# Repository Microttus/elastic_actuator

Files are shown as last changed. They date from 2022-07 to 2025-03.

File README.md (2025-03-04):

# Elastic Arm

This device was developed and tested during the Haptic Summer School
at UiA for the EMERALD project Autum 2022.

*If you are to publish work base don this project please cite:*

```text
@article{sanfilippo2024open,
  title={Open-source design of low-cost sensorised elastic actuators for collaborative prosthetics and orthotics},
  author={Sanfilippo, Filippo and {\O}kter, Martin and Dale, J{\o}rgen and Tuan, Hua Minh and Zafar, Muhammad Hamza and Ottestad, Morten},
  journal={HardwareX},
  volume={19},
  pages={e00564},
  year={2024},
  publisher={Elsevier}
}
```

## Table of Content

1. [Motivation](#motivation)
1. [Demonstration](#Video)
2. [Intro](#the-haptic-arm-lab)
3. [Code](#code)
4. [CAD](#cad)
5. [How To Use Seeeduino](#implementation-of-seeeduino-in-arduino-ide)
6. [How To Use](#how-to-use)
   - [Instalation](#installation)
   - [Test Code Explanation](#test-code-explanation)

## Motivation

The main goal of this project is to create an easy to build and 
assemble haptic installation which can be controlled as a haptic devise. 
This is made possible by the use of a joint with integrated springs. 
A greater displacement of the motor for a smaller amount of force 
compared to a rigid robotic arm is therefore possible. 

For how to use see: [How To Use](#how-to-use)

## Video
This YouTube video shows an example of both Impedance control and Admittance control was tested:
https://youtu.be/x0tvgowaUfE?si=nHkEfITcb-D-KBVI

## The Haptic Arm Lab

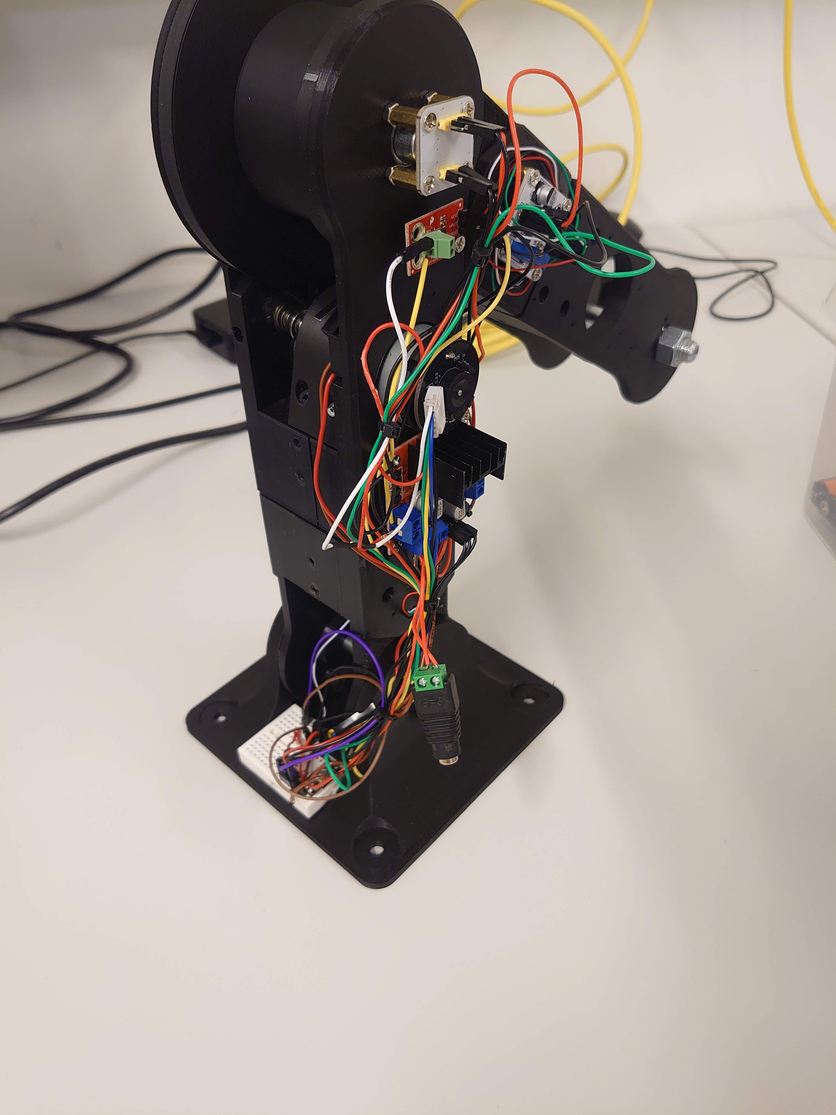
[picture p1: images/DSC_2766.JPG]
Haptic Arm Lab


In Haptic devices, there are two main ways for control. 
Impedance control aim to steer the position by reading the motor force. 
Admittance control aim to control the force of the device by adjusting the position. 
This two are integrated as methods and can be used directly, 
by the use of the low-level libraries this control codes may also be created by the user. 
A descriptive block diagram of the two control loops. 

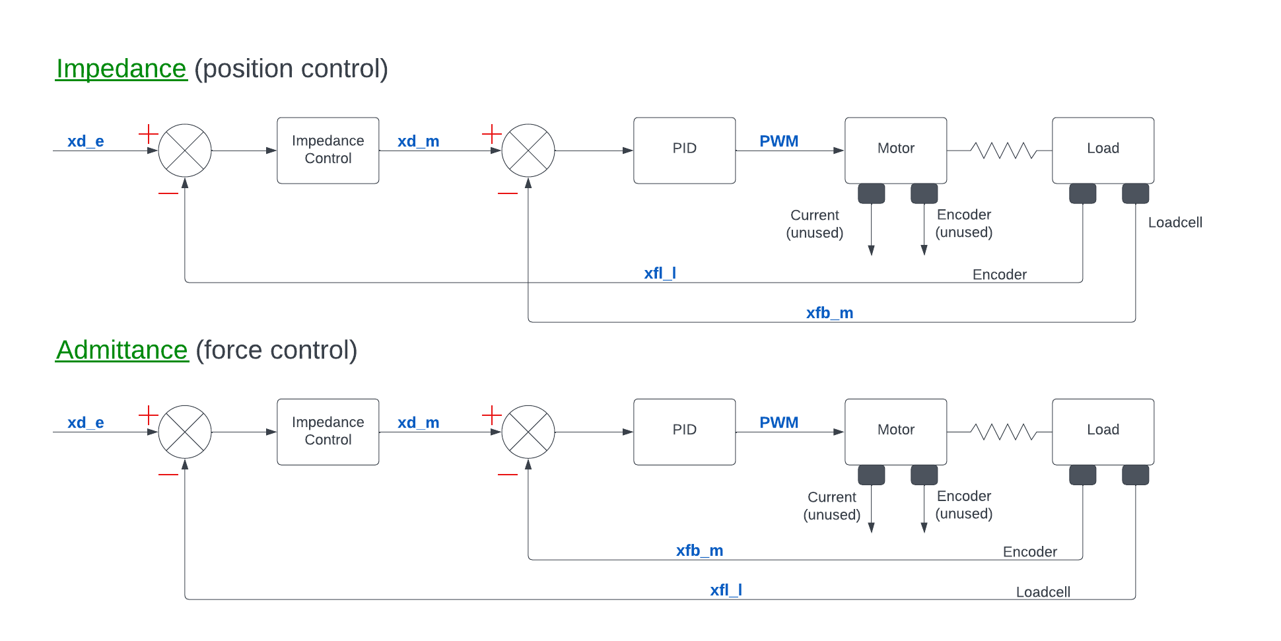
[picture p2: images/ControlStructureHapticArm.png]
Block Diagram


## Code
The code which is to be used can be found in Code.

The main control .ino file can be altered to control the arm in different available modes. The libaries can also be used seperately for control of other mechanical instalation. 

For the Haptic Sommer School course use the studentProgram() implimented into the HapticArm libary for creating own self-produced controlling programs.

For more documentation of the system more detiled information can be found in the documentation folder. (LINK) The documentation is sectioned into mechanical buildt instruction, electrical components and softwear. In addition a more detaiueld explanation of the control theory is available.

The equations used for the control modes are shown beneath.

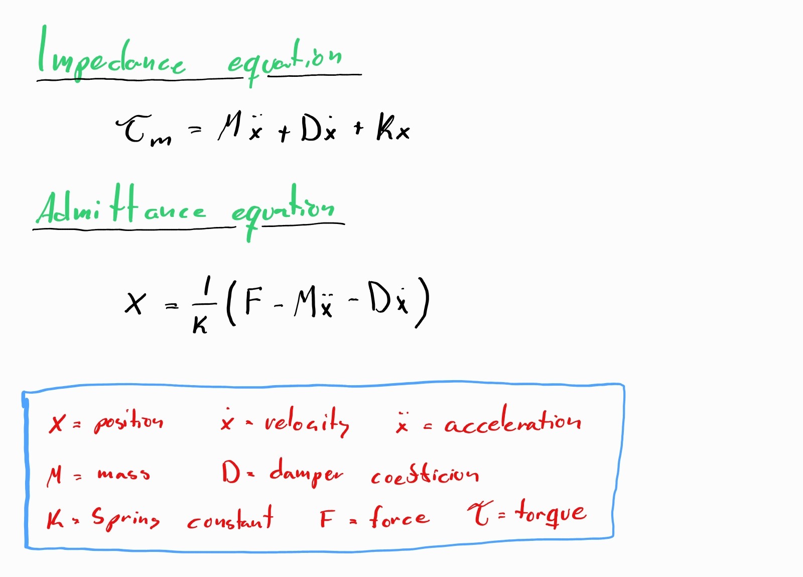
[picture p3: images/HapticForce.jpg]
Force Equations


## CAD
A version off the design can be found in CAD as .stl files ready for printing. In the detailed parts folder the smallest parts and the belt-gear 
which should be printed in higher detail for optimal use, can be found.

## Implementation of Seeeduino in Arduino IDE
To be able to access Seeduino XIAO in the Arduino IDe Board Manager, an "Additional Board Manager URLs:" have to be added in FIle > Preferences:
```
http://files.seeedstudio.com/arduino/package_seeeduino_boards_index.json
```

## How To Use

### Installation

After the complete mechanical assembly is finished and the electronics
mounted as described [here](https://instructions.online/?id=3988-mechanical%20assembly),
the microcontroller of your choice can be plugged into your computer. An IDE for
programming microcontrollers are necessary, the Arduino IDE works perfectly fine and
can be downloaded [here](https://www.arduino.cc/en/software). 

After installing your IDE the seeeduino board programing package have to be added
as described in [Implementation of Seeeduino in Arduino IDE](#implementation-of-seeeduino-in-arduino-ide)
section. 

```text
http://files.seeedstudio.com/arduino/package_seeeduino_boards_index.json
```

Go to Preferences and paste the Url given above into the "Additional board manager URLs:"
box. The seeeduino package should now be available to install from the board manager.

### Test Code

Start by cloning this repository on to your computer. Go to Code->testCode 
folder and open the testCode.ino file in the Arduino IDE. If the microcontroller
is connected, the port should be available in the drop-down menu at the top 
of the window. 

Choose which control method you want to applies by uncommenting the line providing
the selected method. For both ```goImpedance``` and ```goAdmittance``` functions
the three first arguments are respective mass, spring and damper coefficients
for your system. The last argument for impedance is optional and sets the initial
position. If no input are given, 125 degrees, which is the middle, is used. 
The last two arguments for Admittance is optional. The Initial position is 
default middle (125 degrees), and the initial force is 0 that represents the 
force sensitivity of the system. If the initial position is set to -1, the 
arm will hold the current position. This simulates a typical "tech the robot"
mode. 

The ```goPos``` function can be use for basic position control. This function
is used internally in the ```goAdmittance``` and should therefor be carefully 
tuned before moving on to the more advanced control methods. 

### Test Code Explanation

This code provides a basic setup for testing the pre-set control functions.
First, some basic parameters are set up and the hapticArm class used to 
crate an arm object. If any ports on the electronic setup are changed or the 
PID controller needs adjusting, these values can be altered to your preference.

```c++
#include "hapticarm.h"

#include "hapticsensor.h"

// Initiate ports numbers
int motorSetting[5] = {7, 8, 9, 2, 3};    // Pins for motor {forward, backward, PWM, hall_1, hall_2}
int sensorSetting[4] = {1, 0, 6, 10};      // Pins for sensor  {force, current, switch one, switch two}

// PID settings(Kp, Ki, Kd) {position, force, motor} 
float PIDset[3][3] = {{3,3,30},{3,1,0},{0,0,0}};

HapticArm HapArm_(motorSetting, sensorSetting, PIDset);

// Sinus wave
float A = -30;
float B = 0.1;
float dt = 0.0;
```

Every Arduino code contains two functions, the void setup and void loop. 
The setup function is used to setup parameters and input output settings. 
In the test code first a serial port is set up, enabling the serial communication
for feedback to the computer. Additionally, I2C communication is started with 
the ```Wire.begin()``` command. 

The calibration sequence is available in the HaticArm class. 
This actuates the arm to set the correct end switches and
set the encoder values for the end point. This is important since these values
are mapped to the corresponding arm angle which is used for position. 
The encoder limit values are printed in the serial monitor. If the values
are wraped around 0 the encoder chip should be rotated 90 degrees, as wrapping
of the encoder values has not yet been implemented. 

A loop is taken advantage of to set the Arm straight up which provides a 
smoother start for any actuation. This loop is stoped after approximately
10 seconds. Finally a Header to serial monitor with output explanation for the Admittance or
Impedance control function is available. This can be uncommented as needed. 

```c++
void setup() {
  // Initislize importent comunication
  Serial.begin(9600);
  Wire.begin();
  delay(2000);
  HapArm_.calibrateArm(); // If calibration is needed, else should be let out 
  delay(500);

  float curPos = 0;
  float startPos = 125;
  
  // Set arm to middle position
  while (curPos != startPos && dt < 10){
    HapArm_.goToPos(startPos);
    dt = dt + 0.001;
  }
  dt = 0.0;
  
  //Admittance header
  //Serial.println("AcutalPos;SetPos;SpringAngle;Force;RequestedPos;");

  //Impedace header
  Serial.println("AcutalPos;SetPos;MotorReqSpeed;TorqueMes;TorqueCalc;");
  
}
```

The void loop function will constantly run while the microcontroller is powered
on. Here the desired control function is implemented for the Arm object. 
The First line set a sine wave reference which could be used as a set point, for 
instance, seen in the [video](#video). 

The ```goPosition``` uses a basic PID 
control to set the desired position. The ```goImpedance``` function takes 
three required arguments mass, spring and damper coefficient of the system.
Additionally one optional argument can be given, namely the initial position. 
Default is 125 degrees (the middle), but any number between 0–250 can be used. 
The ```goAddmittance``` function takes three required arguments, mass, 
spring and damper coefficient of the system. In addition, two optional 
arguments can be set, initial position and initial force. The Initial position is
default in the middle but can be set to between 0–250. Initial force represents
the force sensitivity and is default 0.

```c++
void loop() {
  // sinewave for setopint reference
  float pos = A*sin(B*dt) + 125;

  // For control with Impedance uncomment this line
  //HapArm_.goImpedance(0, 0, 1);

  // For control with Admittance uncomment this line
  //HapArm_.goAdmittance(0.1,2,0.02,pos);

  // For basic position control uncomment this line
  HapArm_.goToPos(125);
}
```

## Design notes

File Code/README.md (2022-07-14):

# Haptic Arm Code

- The AD5600 libary are used for reading the Rotary Absolutt Encoder via I2C and are created by:
- The PID libary delivers different methods for PID calcuation and are created as objects
- The PWM motor libary are a compleate libary created for controlling a PWM motor in both directions (CW, CCW) and reading a attached incremental encoder
- The HaapticSensor libary are a range of methods for reading the spesific sensores attached to the Haptic Arm
- The HapticArm libary contains a range of methods for compleate control of the Haptic Arm using all the libaries metioned above

## HapticArm Libary

- The goToPos method makes use of a PID controller and the encoders for maintaing the position of the Arm at a sertain deegree from 0
- The goToImpedance method enable for impecace (position - position) control of the Haptic arm, maintaning a requested angle
- The goToAdmittance method enable for admittance (force - position) control of the Haptic arm, maintaning a requested force

- The resistForce makes the arm maintain the given position with the goToPos method until the force barrier given are breached, then the arm gived in and change position
- The goSpring method makes the Arm change its position form the given staring position acting like a spring with the given mass, dmaper and spring constant given
- The calicaration method makes use of the two presure switches for calibration of max and min calibration of the encoder

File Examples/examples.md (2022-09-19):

# Examples

In this folder multiple folders of exaple program testing the reach of the Haptic Arm can be found

In each program the nessesary libaries to add for full operation are lised

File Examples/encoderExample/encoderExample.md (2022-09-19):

# Encoder Example

For reading and adjusting the output of a encoder sensor readings

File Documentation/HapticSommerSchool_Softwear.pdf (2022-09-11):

# 1 Softwear

The software are build as modular as possible, for easy operation of the arm for a user with any programming background. The course are meant to be applied for students with some to none experience in programming and control theory, and at the same time give experienced personnel the possibility to conduct testing of advanced control theory applied. For a less experienced user, the steering library can be used where only the control factor numbers are to be adjusted. A more experienced user may build the control part itself for the implementation of other steering methods. The basic libraries for data collection can be adjusted and modified by an experienced user for optimal control, higher precision and further development of the system.
The software consist of five classes. The AS5600 library is provided by Seed-Studio for easy reading of data from the absolute magnetic encoder. There are three low level classes, the PID, pwmMotor and HapticSensor classes, which are made for data retrieving and control of the haptic arm on a hard code level. The final library, the HapticArm, contains a range of control methods based on control theory using the mentioned classes above for control of the arm.

## 1.1 AS5600

The AS5600 library is created and distributed by Seed-Studio, which is the producer of the encoder used in this project. The data are retrieved using I2C and memory access and the code are therefore manageable but too complicated to learn if you are not interested in the code side. The library gives the user an easy-to-use interface, retrieving the magnets position. This library needs to be put inside the programming folder or the main Arduino library folder for the program to work.

### 1.1.1 getRawAngle()

The getRawAngle is the only method used of this library. The command return the position of the magnet as a 12 bit signal (0-4095).

## 1.2 PID

The PID class are made for easy implementation of PID loops. It takes advantage of the object properties of classes for the user to easily be able to create multiple loops with different PID values based on the same class. The PID class have three public method in addition to the constructor. One which gives the possibility of a standard PID loop using Kp, Ki and Kd and one which provide the possibility of a PID controller with back calculation integration as an anti wind-up method. The last one is a complimentary filter which are used as a low pass filter on the sensor data. The PID method uses the same values and can be switch during operation if needed.

### 1.2.1 PID(float Kp_in, float Ki_in, float Kd_in)

The PID constructor is used to initialize the PID object. The constructor take Kp, Ki and Kd as input and a single PID object are intended to be used for a single PID loop. The values of the PID block cannot be changed during operation.

### 1.2.2 caluclate(float value, float target)

The calculate method is used if a standard PID loop are intended to be used. This method do not have an anti wind-up integrated. The PID equation used are the standard European method, see equation 1.1. The method have the current value intended to be used and the target as input. The aim target may be changed during operation, which is a key feature for the use of control systems.

The loop time is calculated for every loopback by the object for precision loop calculation. This make the object independent of the clock frequency or the loop time. And the code may stagger without the PID failing, taking advantage of the variable loop time calculation.

ud(k) = Kpe(k) + Ki(ui−1 + e(k) · dt) + Kd

e(k) − ud−1
dt | (1.1)

ud is calculated value, e(k) is the error of the system, ui is calculated integral constant and dt the time step.

### 1.2.3 backcalc(float value, float target, float backVal, float satutaionMin, float

saturationMax)

The backcalc method use the same equation as the calculation method, as well as iterate over the same loop time and uses the same Kp, Ki and Kd. These properties make it possible for the user to switch between these two methods. The value are the current value input for the calculation and the target value are the target for the calculation. In addition to these two, the backVal input is used for tuning the anti wind-up section. The saturtionMin and saturationMax inputs are used for the upper and lower limit for the anti wind-up.
The anti wind-up constant could be set to 1 which would work great. This method should be used as the final loop before sending the value to the motor. If this is the case, an upper limit of 255 and lower -255 is advised, corresponding to the upper and lower limit for PWM.
In the backcaluc method, the integral part of the PID calculation are switched with this equation 1.2.

ud(k) = Kpe(k) + Ki(ui−1 + (e(k) + ep(k) − ud−1 T

) · dt) + Kd

e(k) − ud−1
dt | (1.2)

ep is the saturated ud and T is the back calculation value

### 1.2.4 compfilter(float in_val, float alpha)

The compfilter method is integrated as a way to use the equation for complimentary for values. The complimentary filter may be used as a low-pass filter or high-pass filter, depending on the inn-values. A low-pass filter can be essential for readable sensor-data. The in_val are the new data from the sensor used for calculation. A separate PID object should be initialized for every sensor in the system needing a filter. The earlier results are remembered by the object, and the same object cannot be used for different sensor-data. The alpha constant is the tuning value for the filter. This decides how much the new values are to be weighted. This value is set to 0.01 as standard and do not need to be given for this value, unless a different number is to be used.
The method return the final calculated value. The equation used is 1.3.
ud = (1 − α) · ud−1 + α · e(k) | (1.3)

## 1.3 pwmMotor

The pwmMotor class are a collection of different method used for control of a PWM motor using a H-brigde style motor controller and collect data from a hall encoder. The class consist of five public methods in addition to two private ones and the constructor. The two private methods are used for the collection of data as interrupt from the hall encoder and are set to ”static void” as all methods interacting with interrupt variables do need to be of this data type. This is also the reason for the “static void” data type of the reset_hall_val method.

1.3.1 pwmMotor(int forwardPin_in, int backwardPin_in, int pwm_in,
int hallPinOne_in, int hallPinTwo_in)

The constructor of the pwmMotor class have five inputs for correct setup of the connection between the microchip and the motor controller. The first two inputs are the microchip pins, which are to be connected to the directional control of the motor. These pins are used for digital signals. The third is the pin which the PWM signal are sent to. The last two are the pins which the hall sensor pins are connected. Mark: On Arduino Due the only two pins supporting interrupt are 0 and 1.

### 1.3.2 goToSpeed(int motorSpeed)

This method is the main method used for control of the motor. The method receives the motor speed as an integer. Inside the method, the number will be limited to -255 to 255 to ensure the value do not exceed the capabilities of the microchip. The Arduino Due have an 8 bit DAC and these values are preset for this intent, but may be adjusted if a different chip set is to be used.
If motorSpeed is negative the method will spin the motor backward and on the contrary if the value is positive the motor is spun forward. The method also check if the value is equal to the last value asked. The operation of changing direction may be more time conceiving than just adjust the PWM sequence. Checking if the value have changed and immediately break if the value are the same, saves computational time. A value of -1 for backward and one for forward, are additionally commutated and saved for the intent of being able to check the motor direction elsewhere in the code. This is used for the emergency brake.

### 1.3.3 stop()

The stop method immediately set both directional control pin to zero, and then adjust the PWM signal to zero as well. In this configuration, the motor will run free, which is the optimal configuration if the arm have hit something and need to be stopped immediately. This method is used by the emergency break due to endstops, but may also be implemented if the arm is used for obstacle avoidance or as a cobot.

### 1.3.4 check_rotation()

The check_rotation method return the angle of the arms based on the number of trigger events from the hall sensor interrupt routines. While reading the count, the interrupt routine have to be temporarily paused. This means that for every iteration of the method, steps may be missed.

### 1.3.5 reset_hall_val()

This method is used by the calibration method of the arm. At the end of the calibration sequence, the arm is situated at angle 0. Since the motor encoder is incremental, a fixed start position is necessary. The interrupt will start counting as soon as the motor object is initialized, and the count have to be zeroed at a known location. The calibration routine calls this method in the known zero position, which set both trigger event counts to zero.

### 1.3.6 return_motor_dir()

The value saved by the goToSpeed method is internal, and the return_motor_dir method can be called to read the current value. This is used by the end stop emergency stop. The motor direction value is used for the trigger event detection as well.

## 1.4 HapticSensor

The Haptic Arm have five types of sensors which are integrated into the platform. The motor encoder is implemented in the pwmMotor library. The remaining four are the data collected through this library. The AS5600 library is used for the reading of the absolute position encoder. The library consist of five methods in addition to the constructor. Four are the methods for returning sensor data, and the last one is for configuration of the end positions of the arm for the position sensor.

### 1.4.1 HapticSesor(int forcePin, int currentPin, int switchPinOne, int switch-

PinTwo)

The HapticSensor constructor takes four inputs, which are the pins which the sensors are connected to. ForcePin is the pin for the load cell, which has to be connected through an instrument amplifier and are read as an analogue signal. The currentPin is the pin connected to the current sensor, which is read as an analogue signal as well. switchPinOne and switchPinTwo are the pin which the signal side of the endstops. In the constructor, all the input pins are set as inputs, and the analogue read resolution set to 10 bit.

### 1.4.2 readForce()

The readForce method return the force exposed to the end of the arm. The signal read from the load cell is adjusted due to a graph found through testing with known weights at the connection point on the arm. The force is calculated from the weigh and adjusted for the current angle of the arm for neglecting the weight of the swing arm. The value is adjusted with a low pass filter via the PID library before returned as a float.

### 1.4.3 readPos()

The readPos method use the AS5600 library to retrieve the absolute position of the arm from the magnetic encoder. The belonging angle is calculated and returned as a float. The calculation use the values found by the calibration sequence for the value of the magnetic encoder at the endstops.

### 1.4.4 readCurrent()

This method read the value provided by the current sensor, which is situated between the motor and the motor controller. The signal is converted from a bit value into volt and adjusted for the signal at zero current, roughly in the middle. The volt signal is then multiplied with the amp per volt value given for the sensor. A low-pass filter using a PID block are used to smooth out the signal. The current is returned as a float.

### 1.4.5 readSwitch()

The readSwitch method update both values in the list containing the state of the two endstop switches connected. And finally returning these as a pointer to the list. Therefore, the data type int* is used. The list need to be initiated as a class object and not initialized in the object, as the list in that case would be saved in the stack (which is temporary) and removed when the method returns.

### 1.4.6 calibrateEncoder(int newMinVal, int newMaxVal)

The values for the magnetic absolute encoder are saved as object parameters, such that the calibration sequence is not absolutely necessary if the values for a specific configuration are well known. These values are set in the constructor. After the calibration sequence, the found values are used to change these private values by the use of the calibrateEncoder method. The method return the current raw bit value of the magnetic encoder for the intent of using it during calibration. The argument are optional, but the values will be set to 0 if no value is provided.

## 1.5 HapticArm

The HapticArm library is a class combining the lower lever control classes of the Haptic Arm with the intent of controlling the arm using control theory. The library consist of four public and four private methods in addition to the constructor. The of the private method two are calculating the moved length, speed, and acceleration based on the current and part position using numerical mathematics and the same as angles. The mathematics used for the calculation are shown in equation ??. The last two are the emergency protocols witch read data to ensure the arm have a reasonable behaviour and engage the stop routines if not.

### 1.5.1 HapticArm(int motorSettings[ ], int sensorSettings[ ], int PIDset[ ][3])

The HapticArm constructor takes two list and one multidimensional list as input. The first list are the values used to set up the motor object, in total four values. The object for using the other classes are set up inside this class, which means that all necessary values have to be delivered by this object as a middle man. As a way to avoid having 15-20 input for the object, it is initialized with lists. The second list are the values for the sensor class, and need five objects. The constructor do not need to know the size of the list, but enough values have to be given for the constructor to succeed. The third list is a Nx3 matrix, and contains the values Kp, Ki and Kd for all PID objects which are used in the object. The objects are the defined in the constructor as well as other needed constant. One of this is the type of switch used. Original the endstop switches are set to normally closed (NC) corresponding to “1”. If the setup support NO, this would be better, but the Due does not support the needed pull-down resistor.

### 1.5.2 goToPos(float requiredPos)

This method is the basic inner loop of the motor control. It read the position of the arm and adjust the PWM signal sent to the motor, trying to achieve the given required position. This method use the Position PID object, which is the first three values given in the PID matrix. This PID should be the first to be tuned for optimal control of the arm, due to the fact that it is the inner loop for the goAdmittance method. For the PID calculation, back calculation is used for saturation of the signal.

### 1.5.3 calibrateArm()

The calibrateArm method are the main calibrate sequence which check the position of the magnet at the end stops and zero the motor encoder at 0 degrees. By reading both switches during the sequence, the switch located at zero degrees and 250 depresses is mapped, and take care of misplacement of these wires. The motor speed will be manual, set to the minimum safe speed which the arm will be able to rotate.
For visual confirmation of started sequence, the method will print “Calibration started” to the serial monitor. After successful calibration, the maximum and minimal magnetic value will be printed at the serial monitor. This value may be used to adjust the preset values in the code.
The calibration sequence may be left out if the preset values are to be trusted and the motor encoder is not in active use.

### 1.5.4 goImpedance(float massConstant, float damperConstant, float springCon-

stant)

This method enables the user to control the arm using Impedance control, which means reading the movement of the arm and adjusting the output torque of the motor. The private method movedAngle are used to find the radial movement of the arm and the current are read by using the sensor object. The movement values are then multiplied with the mass, spring, damper values, which are given by the user as inputs for the method. The equation used is 1.4.

τ = M ¨θ + D ˙θ + Kθ | (1.4)

The resulting torque is with the read current used to calculate a new speed and feed to the motor. The emergency test is embedded for safety.

### 1.5.5 goAdmittance(float massConstant, float damperConstant, float spring-

Constant, float initialPosition)

This method enables the user to control the arm using Admittance control, which means reading the input force and controlling the position of the arm. The system will act as a spring damper system and centre around the given initial position value. The private method movedLenght is used to find the moved length since last iteration. The length is based on the given length of the arm and uses trigonometry. It is an estimate based on numerical iteration of a curve divided into triangles, and the frequency of the code are important for the validation of the method.
The current applied force are read by the use of the sensor object and the corresponding offset length are calculated using this equation 1.5.

xnew =

F − Dx˙ − Mx¨
K

(1.5)

The calculated length is calculated as angle and applied to the initial angle value. Finally, the required angle is sent to the goToPosition method used for the inner loop. The emergency test is embedded in the goToPosition method.

### 1.5.6 energencyCheck()

The method check the current motor direction and if any of the end stop switches are activated. If one of the switches are activated and the motor direction is pushing the arm further into the switch, the emergency brake is activated. If the motor direction are away from the switch, it is assumed the motor are trying to fix the problem and the break are not activated.

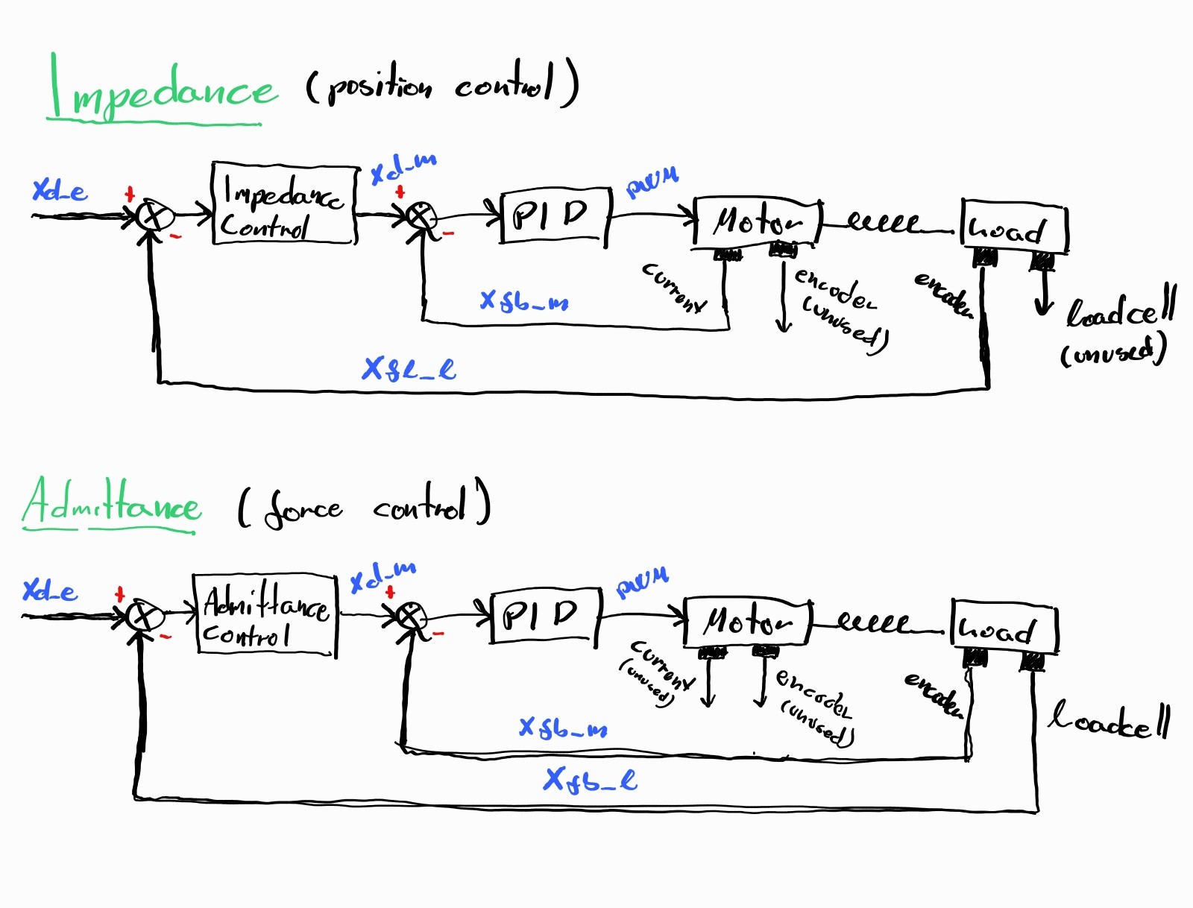
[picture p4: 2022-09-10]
images/AdImpblockdiagram.jpg

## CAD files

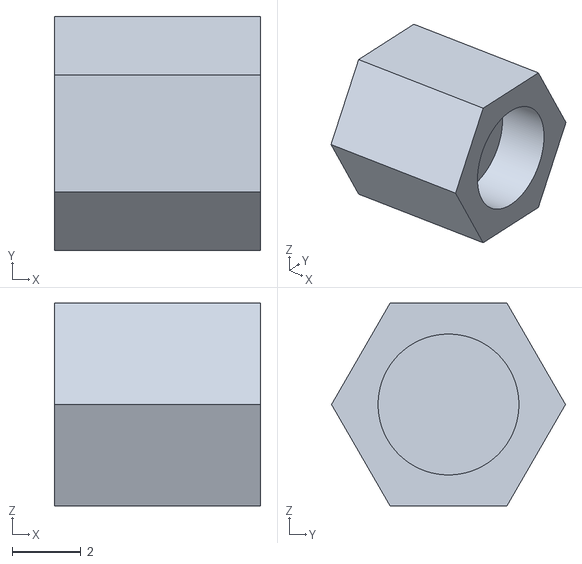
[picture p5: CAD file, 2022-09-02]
CAD/STLs/Detail parts (Markforge)/MagnetHolder.stl
6.00 x 6.81 x 5.90

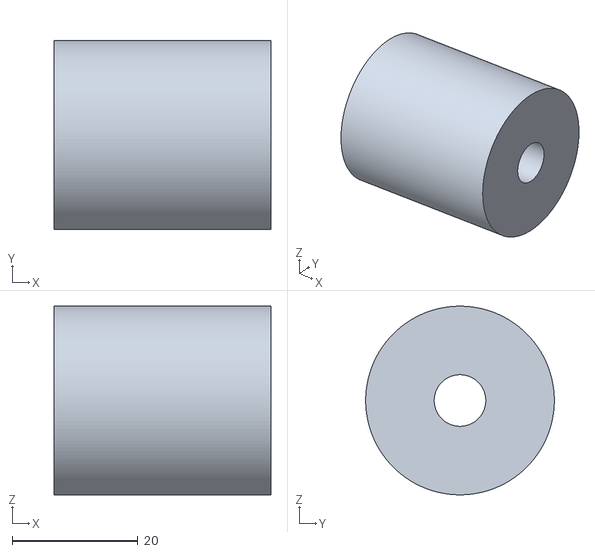
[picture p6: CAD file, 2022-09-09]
CAD/STLs/Joint_L.stl
34.5 x 30.0 x 30.0

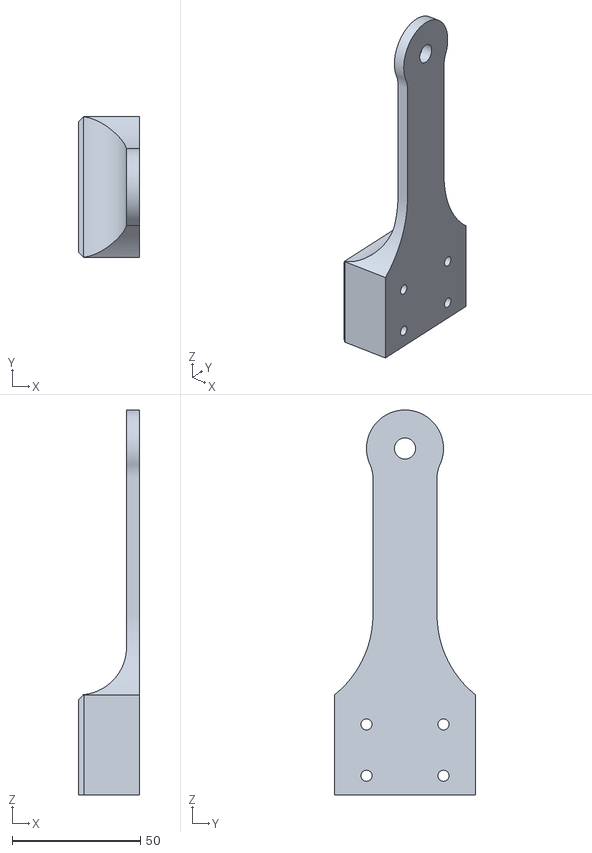
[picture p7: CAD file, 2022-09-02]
CAD/STLs/Tooltip/TooltipLeft.stl
23.7 x 55.0 x 150.0

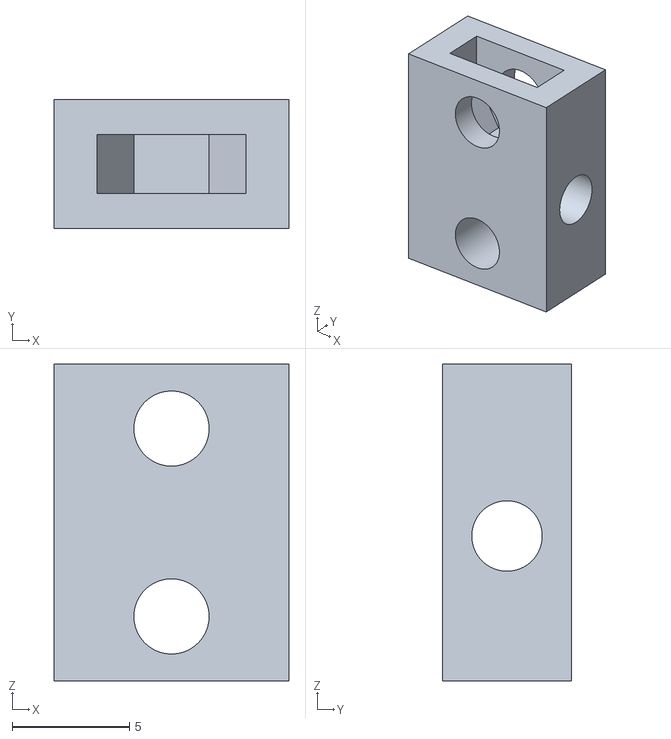
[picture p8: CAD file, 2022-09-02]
CAD/STLs/Detail parts (Markforge)/IdlerCart.stl
10.0 x 5.50 x 13.5

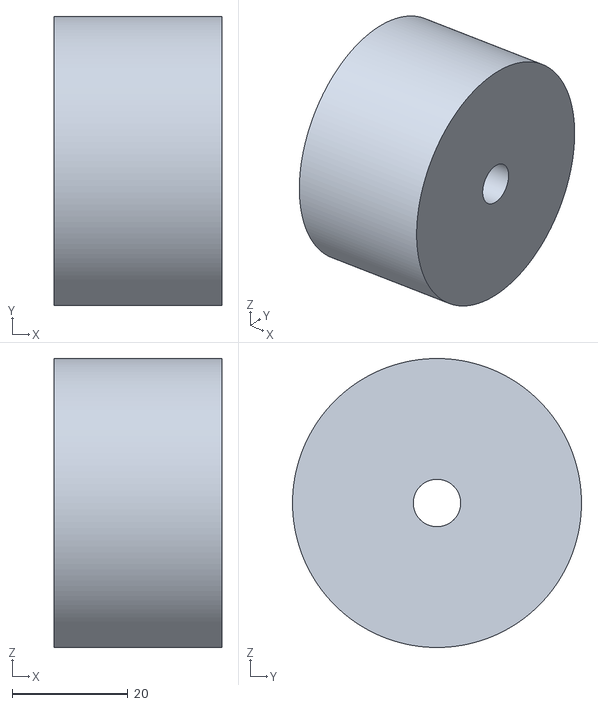
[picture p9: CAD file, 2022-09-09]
CAD/STLs/Joint_S.stl
29.0 x 50.0 x 50.0

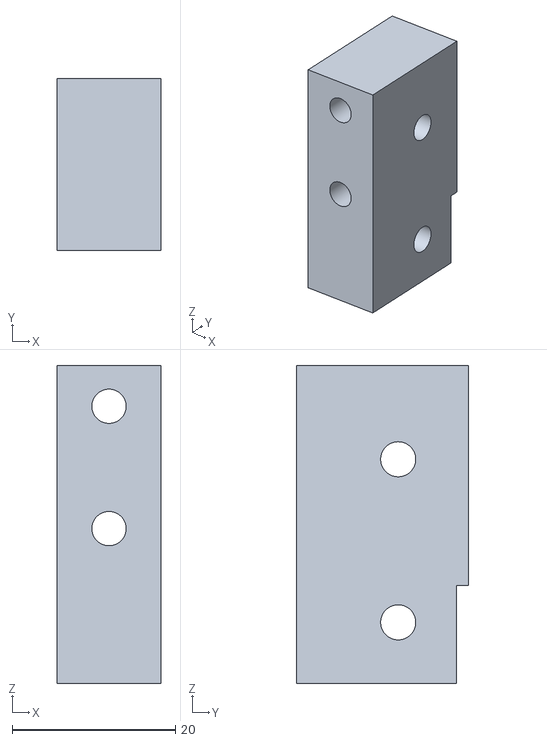
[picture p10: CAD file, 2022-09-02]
CAD/STLs/Tooltip/TooltipSpacer.stl
12.7 x 21.1 x 39.0

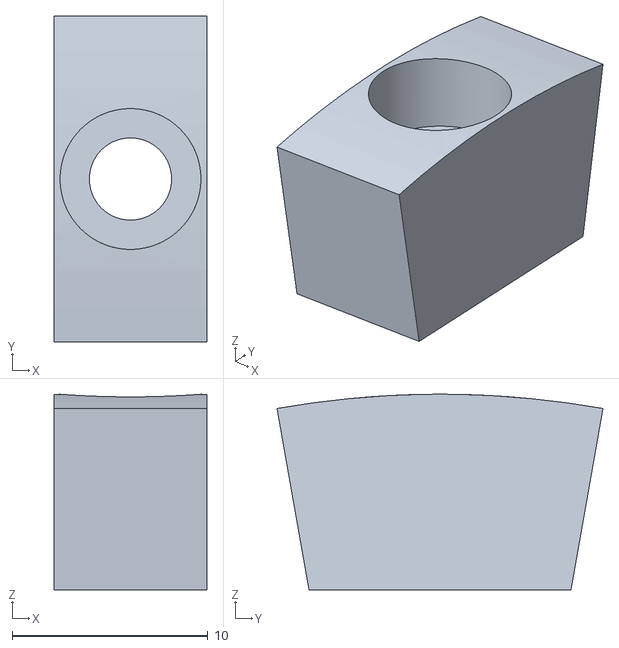
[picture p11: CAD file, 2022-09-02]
CAD/STLs/Detail parts (Markforge)/BeltWedge.stl
7.80 x 16.7 x 10.0

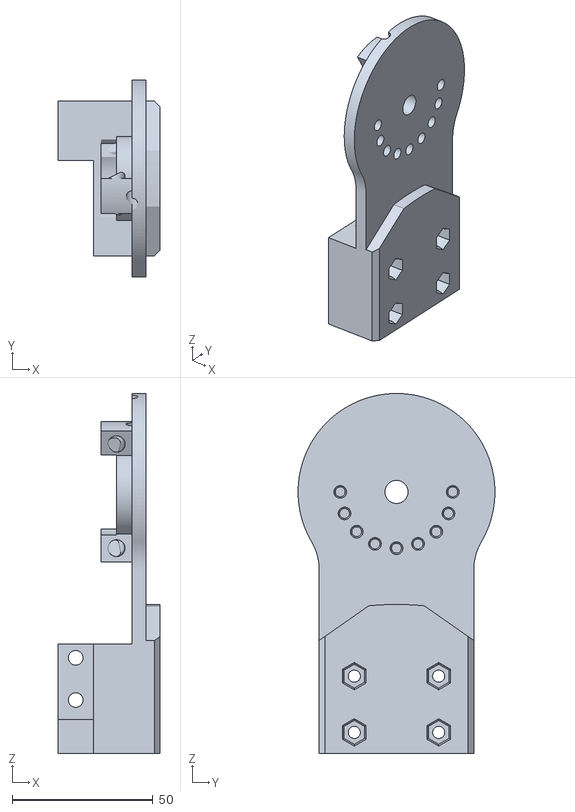
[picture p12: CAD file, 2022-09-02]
CAD/STLs/LowerRight.stl
36.4 x 70.0 x 128.0

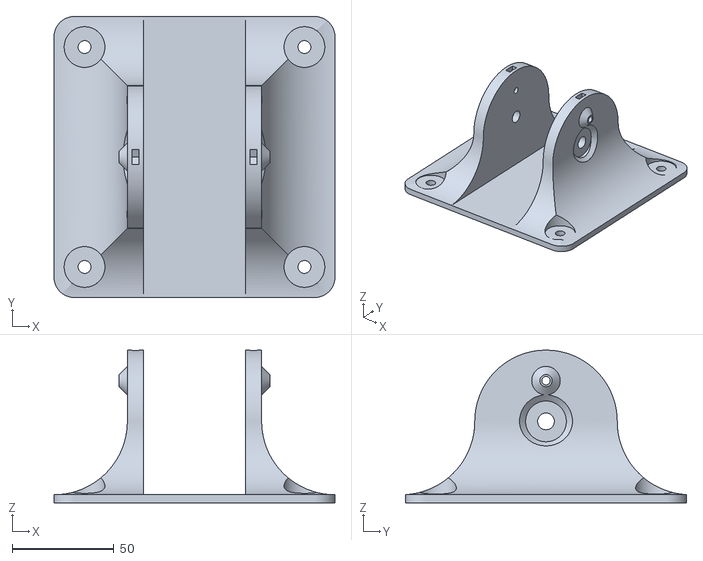
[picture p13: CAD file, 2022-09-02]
CAD/STLs/Base.stl
138.0 x 138.0 x 75.0

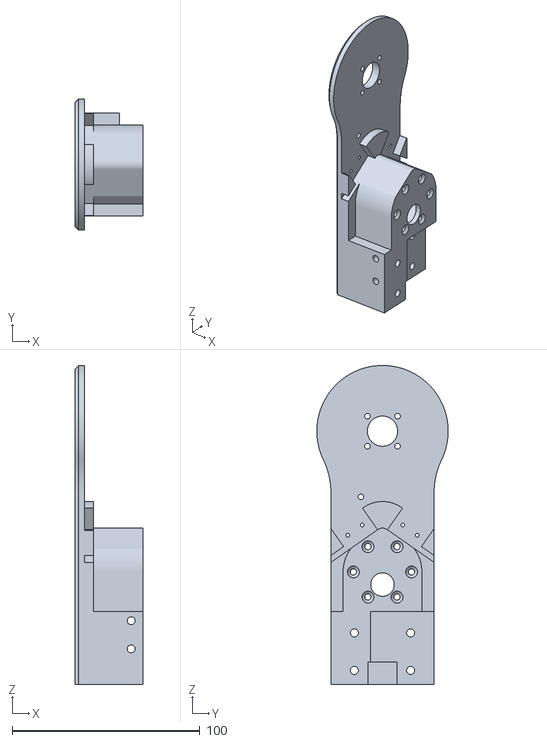
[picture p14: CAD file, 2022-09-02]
CAD/STLs/UpperLeft.stl
36.3 x 70.0 x 170.0

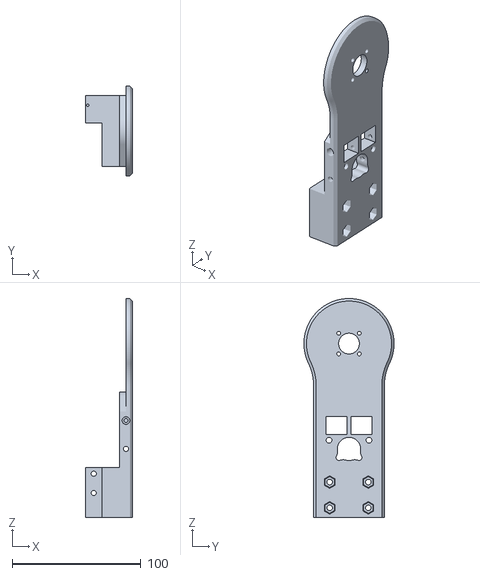
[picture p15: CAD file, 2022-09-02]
CAD/STLs/UpperRight.stl
36.4 x 70.0 x 170.0

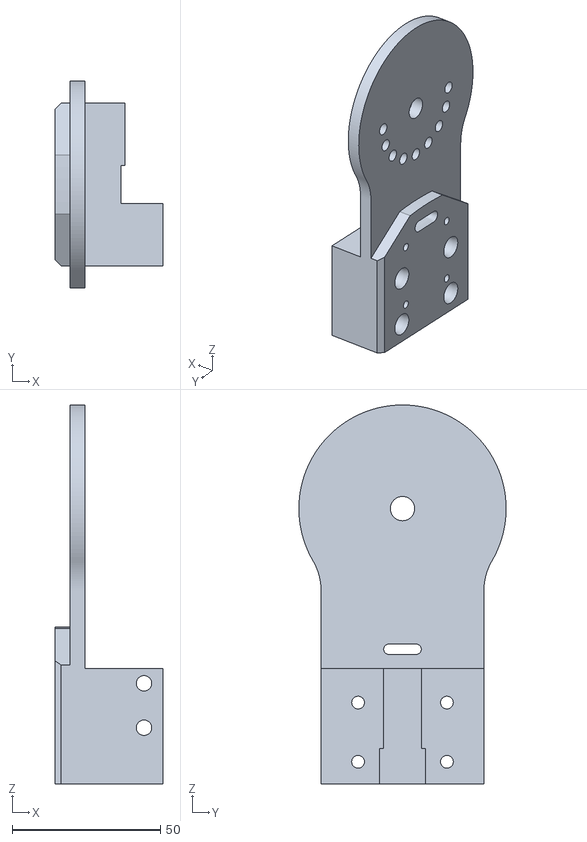
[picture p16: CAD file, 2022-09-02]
CAD/STLs/LowerLeft.stl
36.4 x 70.0 x 128.0

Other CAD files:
CAD/STLs/Tooltip/TooltipRight.stl

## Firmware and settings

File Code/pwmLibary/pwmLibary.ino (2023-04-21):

/*
* Author:
* Microttus
*
* Start code for haptic device testing
*  Buliding the pwm motor liabry for inegrated control
*
*/
#include "hapticarm.h"

#include "hapticsensor.h"

// intitiate ports numbers
int motorSetting[5] = {7, 8, 9, 2, 3};    // Pins for motor {forward, backward, PWM, hall_1, hall_2}
int sensorSetting[4] = {1, 0, 6, 10};      // Pins for sensor  {force, current, switch one, switch two}

float positionPID[3] = {2,0.001,1};       // PID for position {Kp, Ki, Kd}
float motorPID[3] = {1,0,0};              // PID for outer cascade motor {Kp, Ki, Kd}
float forcePID[3] = {2,0,1};              // PID for force {Kp, Ki, Kd} 

float PIDset[3][3] = {{1.4,0.001,1000},{2,0,1},{1,0,0.54}};

HapticArm HapArm_(motorSetting, sensorSetting, PIDset);

void setup() {
  // Initislize importent comunication
  Serial.begin(9600);
  Wire.begin();
  delay(2000);
  HapArm_.calibrateArm(); // If calibration is needed, else should be let out 
  //delay(500);
}

void loop() {
  //HapArm_.goImpedance(0, 0, 1);
  //HapArm_.goAdmittance(1,0,5,125);
  //HapArm_.goToPos(125);

  HapArm_.studentProgram();
}

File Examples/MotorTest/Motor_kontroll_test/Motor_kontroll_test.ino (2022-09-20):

//Define pin numbers
int motorpin1 = 7;
int motorpin2 = 8;
int enablepin = 9;
int buttonpin1 = 6;
int buttonpin2 = 10;

int direc = 1;


void setup() {
  // put your setup code here, to run once:
  Serial.begin(9600);
  
  pinMode(motorpin1, OUTPUT);
  pinMode(motorpin2, OUTPUT);
  pinMode(enablepin, OUTPUT); 
  pinMode(buttonpin1, INPUT);
  pinMode(buttonpin2, INPUT);

  //Pullup
  analogWrite(buttonpin1, LOW);
  analogWrite(buttonpin2, LOW);
  
}

void loop() {
  // put your main code here, to run repeatedly:   
  int PWM = 150;
  //Controlling speed (0 = off and 255 = max speed):
  analogWrite(enablepin, PWM); //ENA pin

  // Read buttons states
  int pinValue1 = digitalRead(buttonpin1);
  //Serial.print(pinValue1);
  
  int pinValue2 = digitalRead(buttonpin2);
  //Serial.print(pinValue2);



  if (pinValue1 == LOW && pinValue2 == HIGH) {
    direc = 1;
    }
  else if (pinValue1 == HIGH && pinValue2 == LOW) {
    direc = 2;
    }

  if (direc == 2) {
    digitalWrite(motorpin1, HIGH);
    digitalWrite(motorpin2, LOW);
    }
  else if (direc == 1) {
    digitalWrite(motorpin1, LOW);
    digitalWrite(motorpin2, HIGH);
    }


}

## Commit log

2022-07-03 Added support for current sensor
2022-07-03 Fix + test
    Fixed bugs and ensured goToPos working with setup
    [hapticsensor.cpp, pid.cpp, pwmLibary.ino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]
2022-07-11 Added support for spring motion
2022-07-12 Minor fixes and goToPos validated
    [hapticarm.cpp, hapticsensor.cpp, pid.cpp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]
2022-07-12 Added Back Calculation method for PID
2022-07-12 Hot fix for calibration ++
    [hapticarm.cpp, hapticsensor.cpp, pwmLibary.ino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]
2022-07-24 Hot fix + added suport for compfilter in PID
    [hapticarm.cpp, hapticsensor.cpp, pid.cpp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]
2022-07-30 Fixes for new physical iteration
    [pwmmotor.cpp]
2022-08-04 Bug fix + new Arduino
    [hapticarm.cpp, pwmLibary.ino]
2022-08-13 Fixes for moving calculating and imp/ad
    [hapticarm.cpp, hapticsensor.cpp, pwmLibary.ino]
2022-09-02 added STLs for all parts
    [Base.stl, BeltWedge.stl, IdlerCart.stl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]
2022-09-09 glemte et par deler
    [Joint_L.stl, Joint_S.stl]
2022-09-20 added motor test
2023-04-21 Added board manager link
2023-04-21 Updated PID ++
